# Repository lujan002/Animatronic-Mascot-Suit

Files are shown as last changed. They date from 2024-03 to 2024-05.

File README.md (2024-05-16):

# Junior-Jay Animatronic Mascot 

Watch overview video [here](https://youtu.be/p1z4z74mzpA)

The scope of this project was to develop a wearable, Disney-style, animatronic suit with actuated facial features for the University of Kansas's flagship line of "Jayhawk" mascots. The project was sponsored by the Mechanical Engineering Department at the University of Kansas, with the primary client being the University of Kansas head mascot coach. The initiative aimed to revolutionize the university's mascot program by incorporating advanced, expressive features into a new mascot called "Junior Jay". The primary requirements outlined by the client included the ability for the mascots to display a wide range of dynamic, real-time facial expressions, like those seen in professionally animated characters. 

<p align="center">
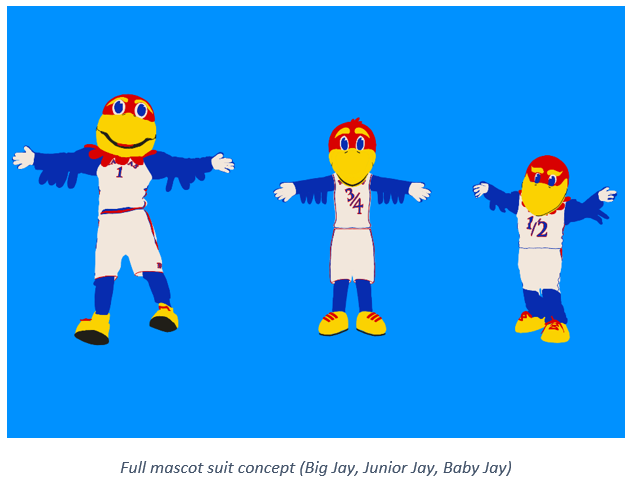
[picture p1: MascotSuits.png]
MascotSuits
  
</p>

Designing an entirely new mascot head from the ground up was not feasible for the financial and time contraints of this project, so the University of Kansas athletics department graciously donated a retired "Baby Jay" mascot head for the team to retrofit into a proof-of-concept prototype for Junior Jay. Without their support, this project would not be possible. 

This project provided a great mix of mechanical, electrical, and software engineering challanges. The engineering objectives were to modify this retired mascot head with seamless control of the mouth, eyebrow, and eyelid actuation mechanisms using custom facial expression detection & control software, while maintaining durability, comfort, and ease of use. The project started in Aug. 2023 with initial drafts of mechanical models, code, and electrical schematics, then concluded in late Apr. 2024 with a functional protoype that met the majority of our project objectives. Below will be an outline of the final state of these three systems. 

<p align="center">
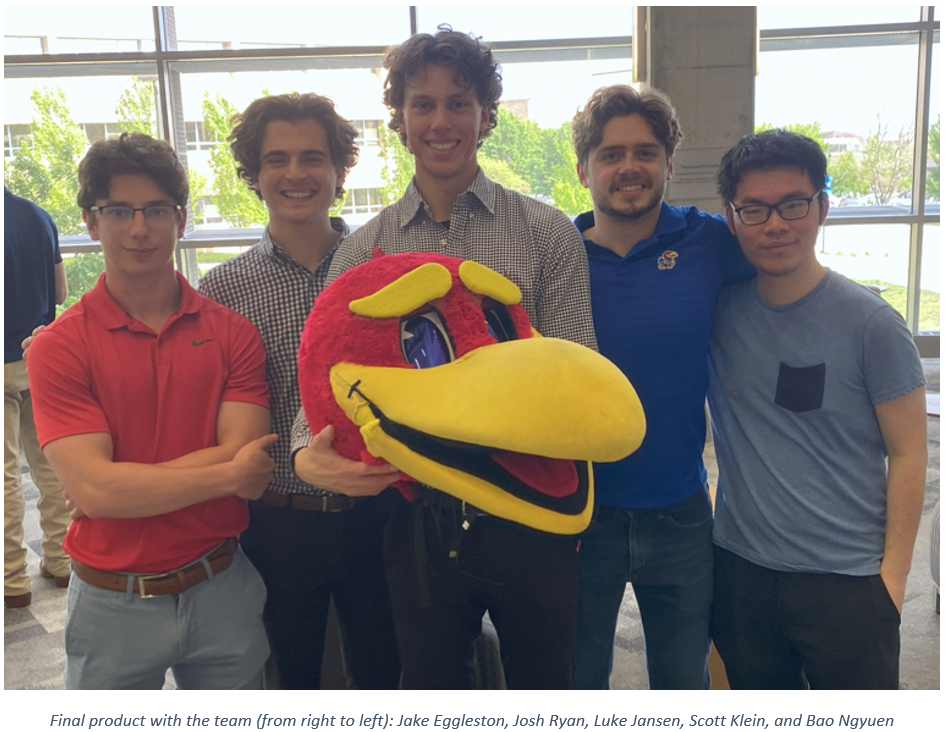
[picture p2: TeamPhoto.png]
TeamPhoto
  
</p>

## Mechanism Sub-Systems
### Beak  

Goal: Open/close beak to simulate smile, shock.

The beak assembly consisted of a lightweight aluminum frame inserted into the original, detached foam beak to provide rigidity and a means for the servo motors to drive the beak. We selected servos rated for 45 kg·cm of torque, suitable for the high-torque demands of our application. This choice was driven by the requirement to counter the beak weight of 0.7 kg (6.87 N), with center of gravity centered 230 mm away (1.58 Nm Torque). After installation, the foam beak was re-stitched to the rest of the head for aesthetic purposes. A primary focus was on ensuring robustness and minimizing weight, and the final frame design shown below was no more than 0.4 kg. 

<p align="center">
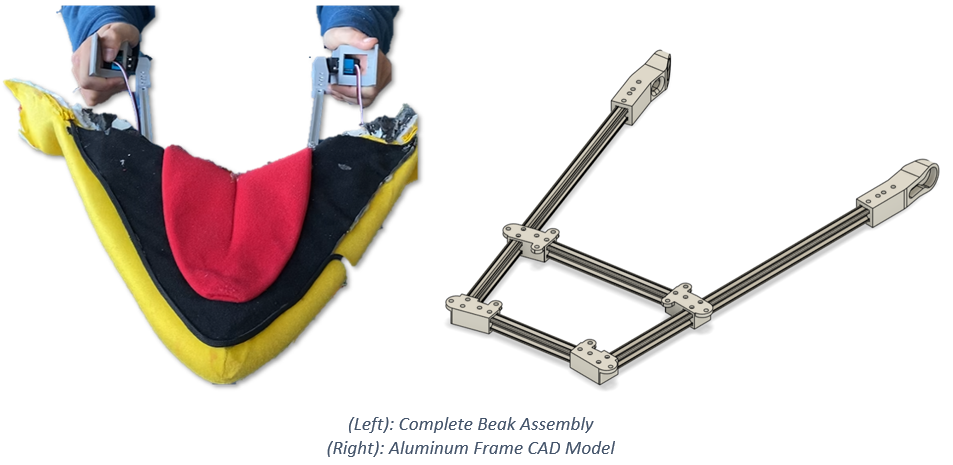
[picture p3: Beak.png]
Beak
  
</p>

### Eyebrows  

Goal: Rotate eyebrows to display nuanced emotions. 

To enable the mascot to express nuanced emotions, precise control over the eyebrows was essential. The final design acheived this by incorporating each eyebrow as one of the links in a three-bar linkage driven by two servos. This gave each eyebrow two ways to pivot, and thus 2 DOF. Each servo connects to one of the other two links, one which keeps its pivot at a fixed distance, and one wich has a slider cutout that allowed for its pivot to translate back and forth. The result is that the eyebrow can raise and lower itself without changing the angle it is oriented at (thus height and angle can be controlled separetely). Given the aesthetic design constraints, the eyebrow actuation mechanisms were concealed inside the head and behind the eyebrow. This in turn necessitated custom-printed shaft extentions so the servo shafts could reach through small holes in the forehead to connect to the links on the outside of the head. Press-fit threaded inserts and a star pattern connection on the shafts ensured the arms did not slip.

<p align="center">
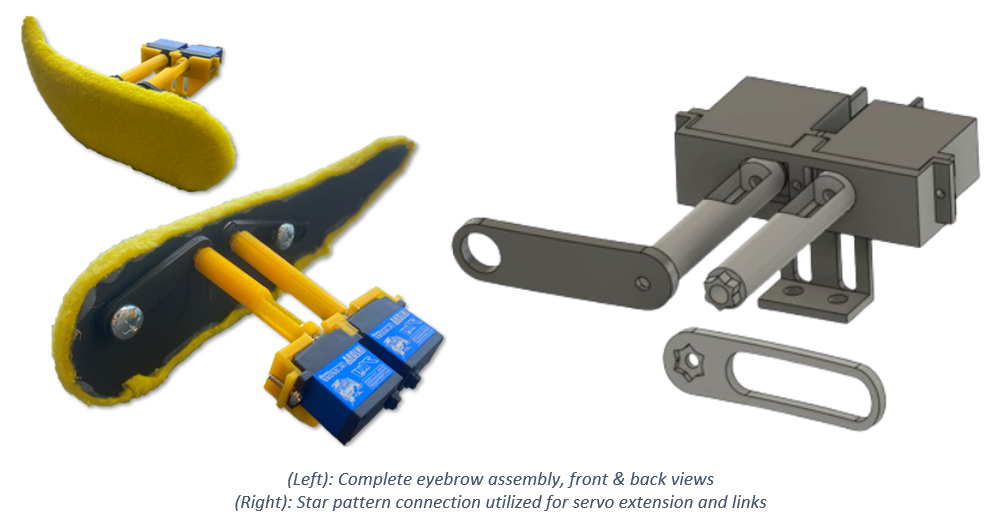
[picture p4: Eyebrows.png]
Eyebrows
  
</p>

### Eyelids  

Goal: Open/close eyelids to simulate blinking.

To enable the animatronics' eyelid functionality, the eyes of the original mascot head had to be removed and offset a small distance to give space for the eyelid fabric to operate. The opportunity to fully rework the eye design was taken. This process involved vacuum forming a PETG plastic sheet over a 3D printed buck, which was then painted with a one-way reflective mirror coating. This new eye was mounted to a frame, along with, conveniently, all the eyelid actuation mechanicms and even the eyebrow servos. This allowed for easy removal of the whole assembly when maintentnce was required. The frame was designed to support the eyebrow mechanics while providing enough space for the eyelid material to spool without increasing in diameter. For eyelid actuation, a compact timing belt system was chosen instead of gears or chains due to its reliability and quiet operation (similar to those used in 3D printers). The eyelid fabric was stiched directly to the belt. 

Initially, a DC motor was considered for this system, but its torque, size, and control limitations led to the selection of a continuous servo motor, which offers sufficient torque and simpler control. To compensate for the servo's slower speed, a gear system was incorporated to increase the speed of the eyelid movement while maintaining the necessary torque for smooth operation. Unlike a normal servo, the continuous servo has no positional feedback. To work around this, two limit switches were added to shut off the motors when tripped. A small object stiched to the belt would trip one switch when the eye was fully open, and the other when fully closed, thus shutting off the motors. 

To better understand how this system works, please watch the docummentation video linked earlier. 

<p align="center">
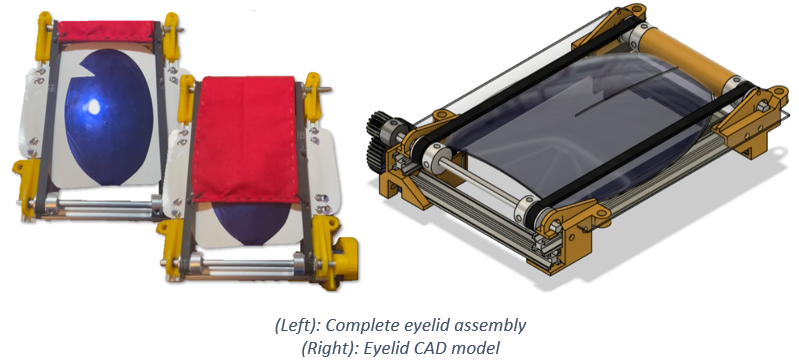
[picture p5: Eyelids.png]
Eyelids
  
</p>

## Expression Detection & Control Software 

Arguably the part of this project with the most innovative potential, and deviation from traditional animatronic models, is the integration of facial detection technology to control the mechanical systems described above. The software algorithm is actually a single “master” python script (master_script.py) running on the Raspberry Pi, which 
handles everything from the capturing of video frames, detection of faces, prediction of a facial expression, and sending of signal to the motors to adjust servo angles to mimic the detected expression.

Early in the development process, it was decided that due to computational limitations of the Raspberry Pi and to avoid jittery mechanical movements, the software would predict discrete emotions and control the motors in set configurations. The emotions to be predicted were "neutral", "angry", "happy", "surprised", and "sad". Separetely, the mouth and eyes would be predicted as "open" or "closed". This approach was chosen over a design that would mimic every nuanced movement of the wearer, prioritizing smooth and stable operation of the mascot.

<p align="center">
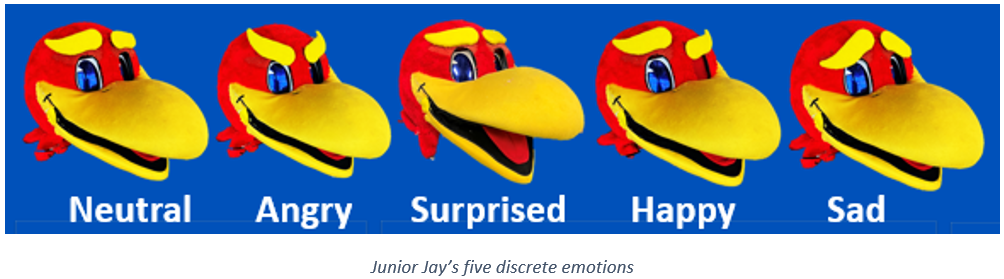
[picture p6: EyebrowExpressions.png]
EyebrowExpressions
  
</p>

The facial detection was naturally split up into different sections based on the mechanical sub-system that it would control. For control of the eyes and mouth, first open-source computer vision libraries were used to extract the coordinates of the facial landmarks (eyes and mouth in this case). Expressions were then classified by measuring the distance between a select few coordinates, such as the outer-most and upper/lower-most mouth edges, and calculating an aspect ratio (mouth height/mouth width). Naturally, when the eyes or mouth are closed, this aspect ratio decreases. Thus, a certain empirically determined ratio was selected and compared with each incoming frames to label the mouth/eyes as "closed" if below the threshold, and "open" if above the threshold. The method implemented in the final master script uses the dlib facial landmark model, although Google's MediaPipe model was also considered.

<!-- Insert EAR,MAR picture here  -->

The movement of the eyebrows, arguably the most important mechanical sub-system in dynamic emotion display, was more intricate. Two approaches were tested for detecting the wearer's emotion out of the five discrete emotions. The first approach used a similar approach to the mouth and eye detection, this time using the eyebrow facial landmark coordinates to come up with some ratio. This posed a more tricky problem that with the eyes and mouth however, as it was quickly realised that predicting emotions based on the eyebrows alone for emotions like sad, happy, and neutral were quite subtle. It would have been possible to combine the eyebrow ratio with a ratio for other landmarks on the face, but ultimately it was decided that a more effective approach would be to use an image classification model to predict discrete emotions. 

A convolutional neural network (CNN) was trained on the [FER-2013 dataset](https://www.kaggle.com/datasets/msambare/fer2013) (Facial Emotion Recognition) to classify facial expressions. The training process is documented in train-emotion-detection.py. The original pre-trained model is attached directly as model_optimal2.h5. This model was converted to a tensorflow.lite model (saved as model.tflite in convert_to_tflite.py), which is directly used in master_script.py. Readers interested in the implementation of this model, its archeture, or the training process are encouraged to reveiw these scripts. The model achieves over 75% accuracy on the validation dataset, with even better performance observed in practical use (potentially a result of the FER-2013 dataset's well-known problem with inconsistent labeling). 

<p align="center">
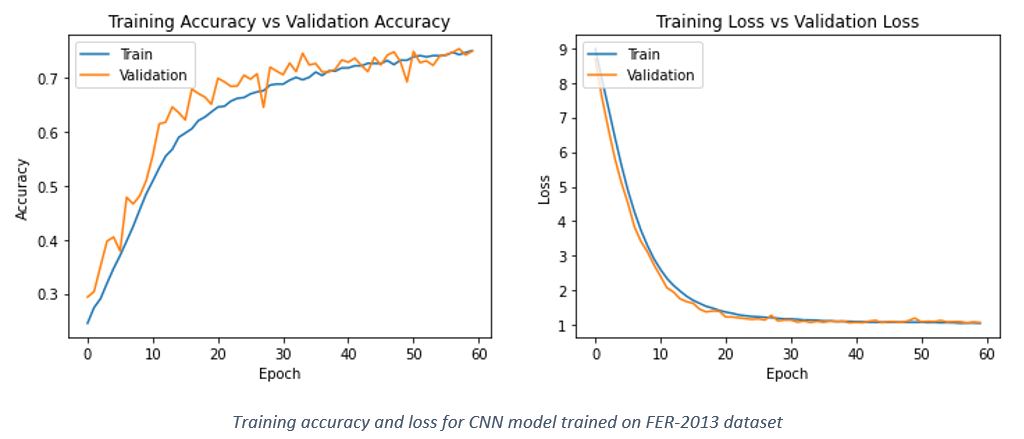
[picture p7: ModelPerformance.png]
ModelPerformance
  
</p>

In order to ensure the program could run as close to real-time as possible, steps were taken to reduce the computational load. One simple approach used was to limit the number of frames processed. Several different frame rates were tested, and ultimately 5 fps was chosen as a nice balance between computational low cost and quick enough updates. The images were also converted to greyscale before processing, which is what the model was trained on and also happens to be more computationally efficient. The model was run using Google’s TensorFlow.Lite library, which is purpose built for running models on lighter hardware. Challenges in detecting faces within the dark, close-up environment inside the mascot's head, even with the use of a low-light, wide-angle camera, hindered the successful demonstration of the internal camera functionality. Efforts to improve face detection under these conditions included enhancing illumination and artificially padding the frame borders to create the illusion of a more distant face. For our demonstration purposes, the camera was positioned outside the head. Future work is required to fully achieve the project's initial objectives under these specific conditions. 

<p align="center">
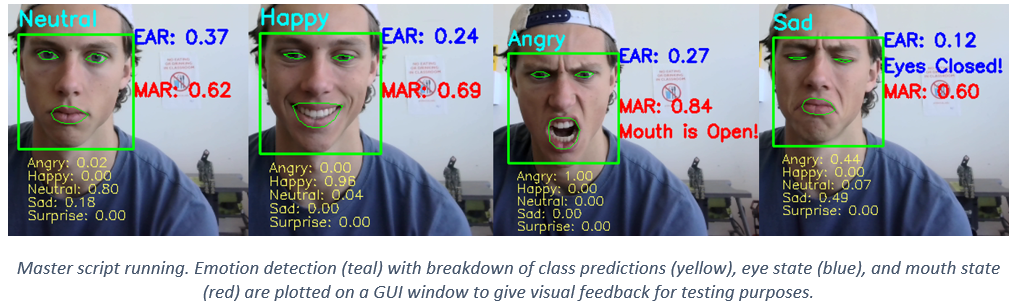
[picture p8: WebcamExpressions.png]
WebcamExpressions
  
</p>

Whatever the approach, signals to the servos were sent from the designated GPIO pins using the pigpio library. 
<!-- Readers can test the standalone software functionality by installing the packages in requirements.txt and runnign software_demo.py -->

## Electrical System

The electrical system composed of 50,000 mAh battery pack specifically chosen for a 2hr. lifetime (or that of a typical basketball game), its three USB type A and C ports, and its 5-20V capacity. This battery choice was driven by the aforementioned 45 kg·cm servos we selected required 9V power to achieve our torque target. Two HUSB238 power delivery breakouts configured to draw 5V and 9V respectively were connected the USB ports on the battery. The Raspberry Pi was directly connected to the third port. In this configuration, all the servos requiring 5V (eyelid and eyebrow servos) were powered separately from the 9V servos (beak servos). Miscellaneous components such as the eyelid limit switches, fans, camera, and LED indicator panel were to be powered by the Raspberry Pi.  

There were two key considerations when designing this system. This system contains approximately fifty loose wires, and it quickly became apparent that wire management was crucial for easy maintenance, visibility inside the head, and ensuring the integrity of the sensitive wiring. All wires were strategically routed around the internal structure of the head. Wires were systematically braided and grouped by sub-system, labeled, and secured to prevent obstruction of vision, reduce tangling risks, and simplify maintenance procedures. A Raspberry Pi GPIO pin extension board with screw clamps was used and gave much needed easy accessibility when pulling and plugging wires. A power bus was designed and implemented that handled the distribution of power to all motors in a convenient location. Since these electrical components would be operating very close to a human’s face, safety was also a top priority. Initial testing done on the 9V beak servos under high load produced worrying results on the multimeter. In some cases, the current draw of an individual servo could spike to well over 1A. To prepare for dangerous current spikes like this, two 1Ω power resistors in series were added to the 9V rail on the power bus to dissipate any excess current as heat. An emergency safety switch was also added to shut the 9V motors off.  

<p align="center">
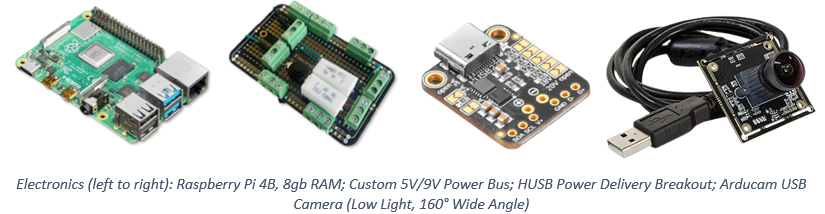
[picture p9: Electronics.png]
Electronics
  
</p>
<p align="center">
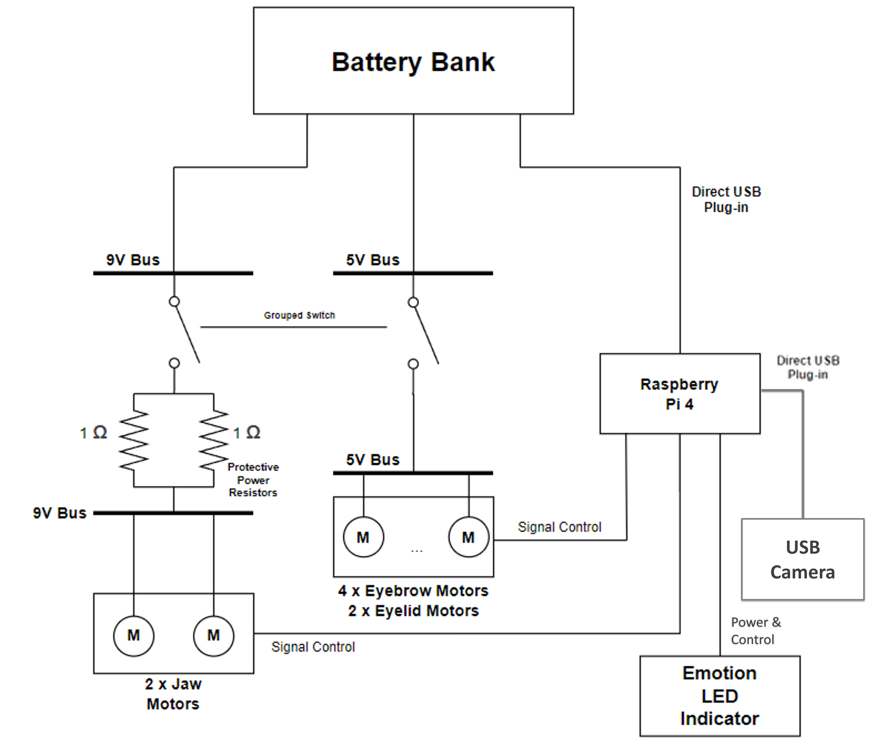
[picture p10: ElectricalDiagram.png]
ElectricalDiagram
  
</p>

### Voltage Converter PCB
The servos that move the lower beak were chosen for their high torque at operating volages above 5V. The servos used were actually rated for 5V - 8.4V, so initially a voltage converter circuit was designed to step down the input voltage to 8V. Later it was realized that the servos could run on 9V directly from the power bank, making this voltage converter irrelevant. Regardless, an short summary of the work done on it will be listed. A [dummy breakout](https://www.adafruit.com/product/5807) was used to draw 12V from the [power bank](https://www.amazon.com/Charging-50000mAh-Portable-Compatible-External/dp/B0C5D1JR2K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), which was further stepped down to 8V by this circuit. 

The schemetic shown below incorporates an [LM317 Voltage Regulator](https://www.ti.com/product/LM317-N/part-details/LM317T/NOPB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) ([footprint](https://www.snapeda.com/parts/LM317T/NOPB/Texas%20Instruments/view-part/)) and a series of commonly available resistors.

The board was designed in KiCAD and printed at the school shop.

<p align="center">
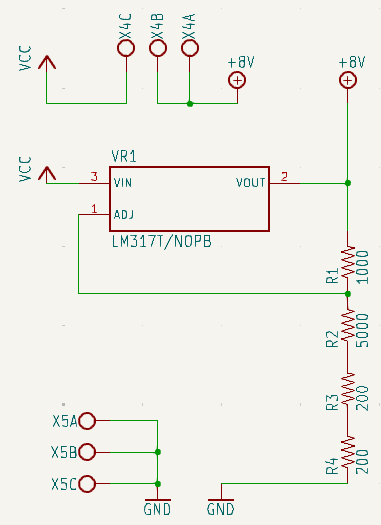
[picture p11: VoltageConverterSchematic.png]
VoltageConverterSchematic
  
</p>
<p align="center">
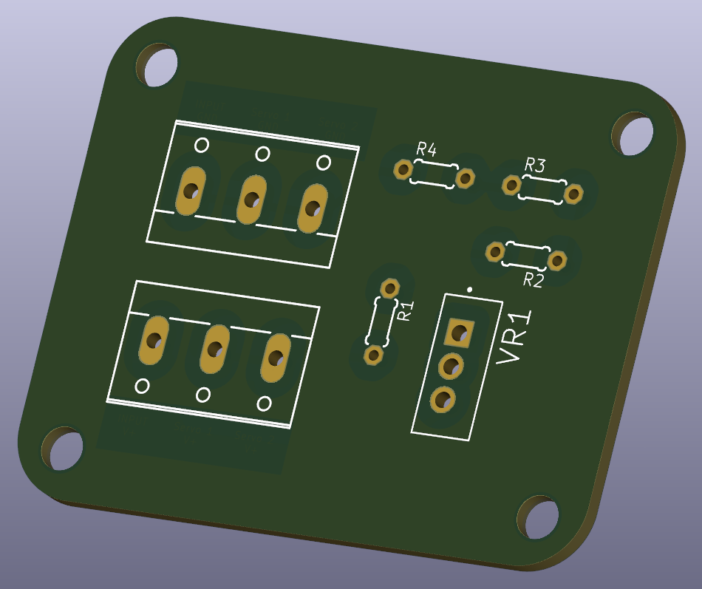
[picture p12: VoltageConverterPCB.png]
VoltageConverterBoard
  
</p>

### Emotion LED Indicator Panel
One concern during operation of the animatronic was that the wearer would have no idea what expression was currently being used. The beak and eyelids would be obvious enough to the wearer if they were open or closed, but there would be no way of knowing the current state of the eyebrows. An LED panel indicator panel was designed as a solution to this. The panel was planned to be mounted inside the head and include seven LEDs, five for each of the discrete emotions, one LED for the mouth state, and one for the eye state. This would tell the wearer inside if the expression detection program is working as intended. Ultimately time constraints prevented the implementation of this optional feature, but the concept was proven to work. 

The board was designed in KiCAD and printed at the school shop.

<p align="center">
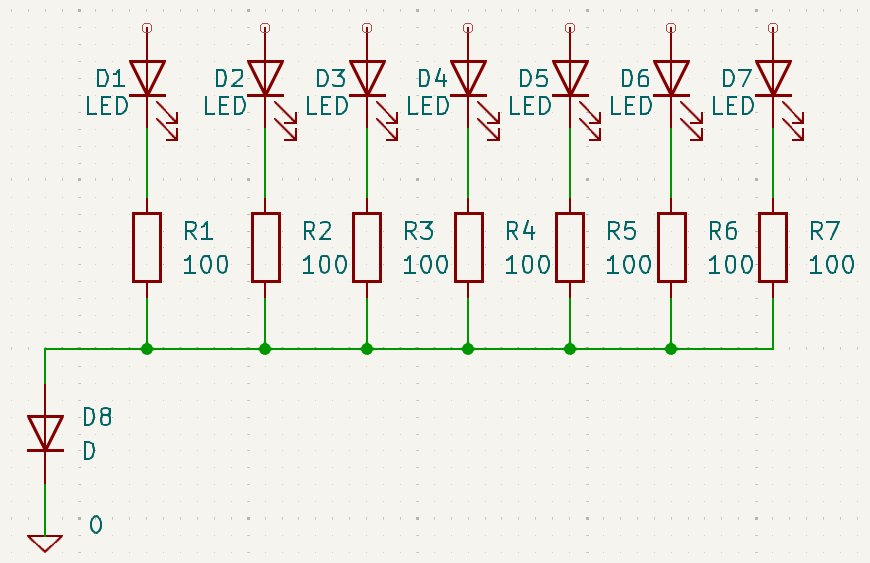
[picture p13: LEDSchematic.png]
LEDSchematic
  
</p>
<p align="center">
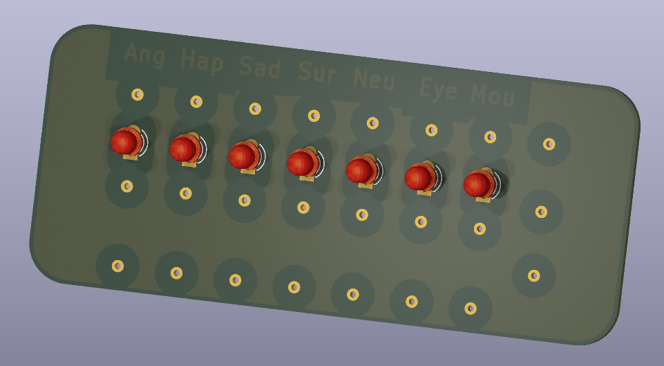
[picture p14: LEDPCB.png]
LEDPCB
  
</p>

### Future Work

While the project has made significant strides in demonstrating that the functionality and appeal of university mascots can be dramatically improved, there remains scope for further development to fully realize the envisioned goals. Future work could focus on several areas to refine and expand the project's achievements: 

1.  Refinement of Mechanical Systems: Further refinement of the mechanical systems controlling facial expressions is essential. Continuous testing and iteration could lead to more fluid and natural movements, reducing any mechanical lag or stiffness currently present. 
2.  Advanced AI and Machine Learning: Implementing more sophisticated AI algorithms and machine learning techniques, such as training on a larger dataset or a custom dataset built to our specific needs, could enhance the accuracy and responsiveness of the facial recognition system. Also, work can be done to give more nuanced expressions prediction rather than the simpler discrete expression approach used. This would ensure a more precise and seamless translation of the performer’s expressions to the mascot. 
3.  Enhanced Cooling Technologies: Although the current cooling system provides basic relief, exploring advanced technologies like phase change materials or more efficient heat exchange mechanisms could offer better temperature regulation, increasing comfort during longer performances or in more extreme weather. 
4.  Integration of Interactive Technologies: Adding interactive technologies such as voice modulation and responsive sound systems could make the mascots even more engaging. For instance, allowing the mascots to respond vocally to crowd interactions or integrate sound effects linked to their movements could greatly enhance audience interaction. 
5.  Sustainability and Materials Science: Investigating more sustainable materials and construction techniques that maintain durability while reducing weight could improve the ergonomics and environmental impact of the mascot costumes. 
6.  Extended Wearability Studies: Conducting extended wearability studies to gather data on the performer's comfort and suit ergonomics over longer periods can provide insights into necessary adjustments and improvements. 
7.  Scalability and Transferability: Finally, considering how these enhancements can be standardized and transferred to other mascot programs could broaden the impact of the project. Developing a modular system that can be customized and adapted to different mascots could make these advancements more accessible to other institutions. 
8.  Foolproof electrical safety measures: A mechanical cover should be added to cover the power bus to protect against accidental contact and reduce the risk of short circuits. Additionally, wiring may be optimally routed inside the head wall to minimize exposure and vulnerability. Safety devices such as fuses, and micro-circuit breakers will be incorporated to prevent electrical overloads and potential hazards.  

These areas of future work would not only address the remaining challenges, but also push the boundaries of what is possible in mascot design and performance - potentially setting new industry standards. 

For a full detail of the technical work involved in the project, please refer to the "Junior Jay Final Poster" and "Junior Jay Final Report" documents.

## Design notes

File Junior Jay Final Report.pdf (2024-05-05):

Title: Junior Jay Capstone Project Sponsor: The University of Kansas School of Engineering Mechanical Engineering Members: Scott Klein, Luke Jansen, Josh Ryan, Jake Eggleston Electrical Engineering Members: Caleb Meyer, Bao Nguyen, Josie Harding

1

## Table of Contents

Figure 1. Use This Format to Label All Figures!! | Error! Bookmark not defined.

Electrical Engineering Members: Caleb Meyer, Bao Nguyen, Josie Harding

2

## Executive Summary

### Motivation

After observing the KU mascots in action, two members of our project sent a proposal to the University of Kansas on June 23, 2023, seeking to enhance the Big Jay and Baby Jay mascots by adding Disney-like animated features and a liquid cooling garment for performer comfort. This initiative aimed to boost the mascots' appeal during key events like March Madness. However, the head mascot coach suggested creating a new mascot, Junior Jay, for the kids club of Kansas Athletics, to preserve the originality of Big and Baby Jay.

### Engineering Objectives

In response to the head mascot coach's suggestion, our team planned to integrate AI-driven facial recognition technology with mechanical systems for the Junior Jay mascot. This setup would detect and mimic the facial expressions of the person inside the mascot head in real time, translating them into movements of features like eyebrows, eyelids, and mouth via actuators and linkages. This combination of AI and mechanical engineering aims to enhance the mascot's expressiveness and ensure performer comfort during events.

### Technical Approach

To achieve our project goals, our group met weekly throughout the spring semester to develop and refine the designs for the mechanical movements needed to animate the mascot's facial features. We took a prototype and testing approach to develop Junior Jay for this project. To do so, servo motors and 3D-printed linkages were utilized and optimized for seamless integration and effective operation. During the installation phase, we performed additional redesigns to ensure the components fit well within the mascot head while maintaining comfort and wearability for the performer. This iterative design and testing process was vital for balancing functionality and user comfort.

### Results

We successfully met most of our objectives for enhancing the mascot's features, although we encountered challenges with achieving full functionality of the eyelids due to software bugs and mechanical unreliability. In the last few weeks of the project, our team intensified our efforts, focusing closely on collaboration and problem-solving to finalize the enhancements. Our result was a functioning animatronic Junior Jay with facial recognition capabilities. Despite the issues with the eyelids, our commitment in the final stages ensured that the rest of the features, including the expressive eyes and integrated cooling system, were implemented effectively. This teamwork and determination were crucial in bringing our innovative mascot enhancements to near completion, significantly elevating the mascot's functionality and appeal.

### Summary

Our project achieved substantial progress in enhancing the mascot's animated features, though some challenges, like the full functionality of the eyelids, remain. Recognizing the potential to fully realize our vision, we submitted a proposal to continue our work, aiming to deliver a completely functional mascot head. This ongoing effort will focus on resolving existing issues and refining the design to ensure it is event ready. We recommend future teams prioritize software optimization and consider further

Electrical Engineering Members: Caleb Meyer, Bao Nguyen, Josie Harding

3

ergonomic adjustments to improve performer comfort. These steps will help in achieving a pioneering mascot presence at university events, greatly enhancing both performance and spectator experience.

Electrical Engineering Members: Caleb Meyer, Bao Nguyen, Josie Harding

4

## Introduction

### General

This project was sponsored by the Mechanical Engineering Department at the University of Kansas, with the primary client being the KU mascot coach. The initiative aimed to revolutionize the university's mascot program by incorporating advanced, expressive features into the Big Jay and Baby Jay mascots. Inspired by the intricate articulation of iconic characters such as Disney's Mickey and Minnie Mouse, the enhancements were intended to include a range of animated facial expressions and integrated cooling systems to ensure performer comfort during performances, especially in warm conditions. This effort aligns with the university's broader goals of enhancing school spirit and audience engagement during athletic events and other university functions. The project's strategic objective was to significantly elevate the visibility and interactive capability of the mascots, thereby enriching the fan experience and potentially increasing student and community involvement with Kansas Athletics.

### Motivation

The motivation for this project stemmed from a desire to enhance the interactive capabilities and overall appeal of the University of Kansas mascots, Big Jay and Baby Jay, as expressed by the client, the KU mascot coach. The primary requirements outlined by the client included the ability for the mascots to display a wide range of dynamic, real-time facial expressions, like those seen in professionally animated characters. This enhancement was aimed at fostering a more lively and engaging presence at university events, thereby deepening the emotional connection between the mascots and the audience. Additionally, the client emphasized the need for improved comfort for the mascot performers, particularly during the intense heat often experienced during early season football games and other outdoor activities. This led to the requirement for integrating advanced cooling technologies within the mascot suits, specifically through the development of a Liquid Cooling Garment system that could maintain a comfortable temperature for the performers over extended periods.
These enhancements were expected to boost the morale and performance of the mascot team and to serve as a pioneering model for other universities looking to upgrade their mascot programs. The overarching goal was to create mascots that are not only emblematic of KU spirit but also stand out on a national level during high-visibility events such as March Madness, thereby attracting more attention and potentially increasing enrollment and fan support. This project was also seen as a strategic move to innovate within the realm of collegiate mascots, pushing the boundaries of mascot interaction and performance.

Electrical Engineering Members: Caleb Meyer, Bao Nguyen, Josie Harding

5

### Engineering Objectives (or Project Design Requirements)

The engineering objectives for this project were defined to directly address the customer requirements and ensure a high level of performance and innovation in the mascot enhancements. The primary design requirements included:

1. Facial Expression Animation: The mascots needed to be capable of displaying a variety of facial expressions that mimic human emotions. This required the development of a sophisticated mechanical system within the mascot heads, utilizing servo motors, sensors, and 3D-printed components to animate features like the eyebrows, eyelids, and mouth in real-time.
2. Facial Recognition Integration: To achieve real-time mimicry of the performer’s expressions, an AI-driven facial recognition system was required. This system would interpret the performer's facial expressions captured via an internal camera and translate them into mechanical movements, ensuring that the mascot's external expressions reflect those of the performer inside.

### 3. Cooling System Implementation: Given the physical exertion and heat exposure during

performances, integrating a Liquid Cooling Garment (LCG) was essential. This system needed to be seamlessly incorporated into the mascot suit, providing efficient heat exchange without adding significant weight or restricting the performer's movements.
4. Durability and Comfort: All enhancements had to be designed with durability and comfort in mind. The mechanical components and cooling systems needed to withstand the rigors of performances and be easy to maintain. Moreover, the overall design had to ensure that the weight distribution and ergonomics of the mascot suit did not compromise the performer’s comfort or mobility.

### 5. Ease of Use and Maintenance: The systems developed for the mascots needed to be user-

friendly, allowing quick adjustments and repairs if necessary. This was crucial for ensuring that mascot handlers could manage the technology effectively during events without requiring specialized knowledge.

These engineering objectives were crafted to create a mascot experience that was not only more engaging and enjoyable for audiences but also more manageable and comfortable for performers, setting a new standard for mascot design in collegiate sports.

Electrical Engineering Members: Caleb Meyer, Bao Nguyen, Josie Harding

6

## Technical Work

### Technical Approach

Our team took a general engineering design approach with this project. Throughout the project, our team met in weekly meetings to discuss and design Junior Jay. Phase 1 included concept design where our team defined the problem statement, product design specification, engineering objectives, and concepts to satisfy those engineering objectives. Phase 2 involved embodiment design where Junior Jay was broken down into three sections: mechanical, electrical, and software. Mechanical systems included design of the beak, eyebrows, and eyelids. Electrical systems included development of the main CPU being the Raspberry Pi, power, power block, and camera. Software included facial recognition to input facial expression signals and output a signal to the mechanical system. With these three sections, modeling, sizing of parts, prototyping, and testing occurred. Our team designed, iterated, and tested Junior Jay was fully functioning. Lastly, phase 3 included detail design where all the sections of Junior Jay were finalized installed into the head as a final product.

### Experimental Setup / Numerical Setup / Designs

Beak
In the design of the mechanical mechanisms for our animatronic Jayhawk head, a primary focus was on ensuring robustness and minimizing weight. One critical component was the beak actuation mechanism, which required careful consideration due to the forces involved, particularly gravity. The beak assembly (figure 1) consisted of an aluminum frame inserted into it to provide rigidity and a point for the servo motors to drive the beak. To achieve reliable operation, we selected servo motors capable of delivering high torque. Specifically, we used servos rated for 45 kg·cm of torque, suitable for the demands of our application.
The beak itself has a mass of 0.36 kg (Figure 3), and the aluminum frame increased the mass to 0.7kg. Through a simple finger-balance test, we determined its center of gravity to be approximately 230 mm (9 inches) from the motor's pivot point. Given this configuration, the required torque to move the beak was calculated as follows:
Torque τ is given by τ = r · F, where r is the radius (distance from pivot), and F is the force due to gravity acting on the mass.

Converting the mass of the beak into weight using the acceleration due to gravity (g=9.81 m/s^2):

F = m · g = 0.7 kg · 9.81

m
s

= 6.87 N

The lever arm r is 0.230 m (230 mm). Thus, the required torque is:

τ = 0.230 m · 6.87 N = 1.58 N · m

Electrical Engineering Members: Caleb Meyer, Bao Nguyen, Josie Harding

7

Each servo, providing 4.41 Nm (45 kg·cm), and with two servos employed, yielded a total available torque of 8.82 Nm (90 kg·cm). This is significantly more than the required 1.58 N·m, ensuring that the servos can operate the beak with high reliability and responsiveness, even under additional load, external forces, or in the event one motor fails.

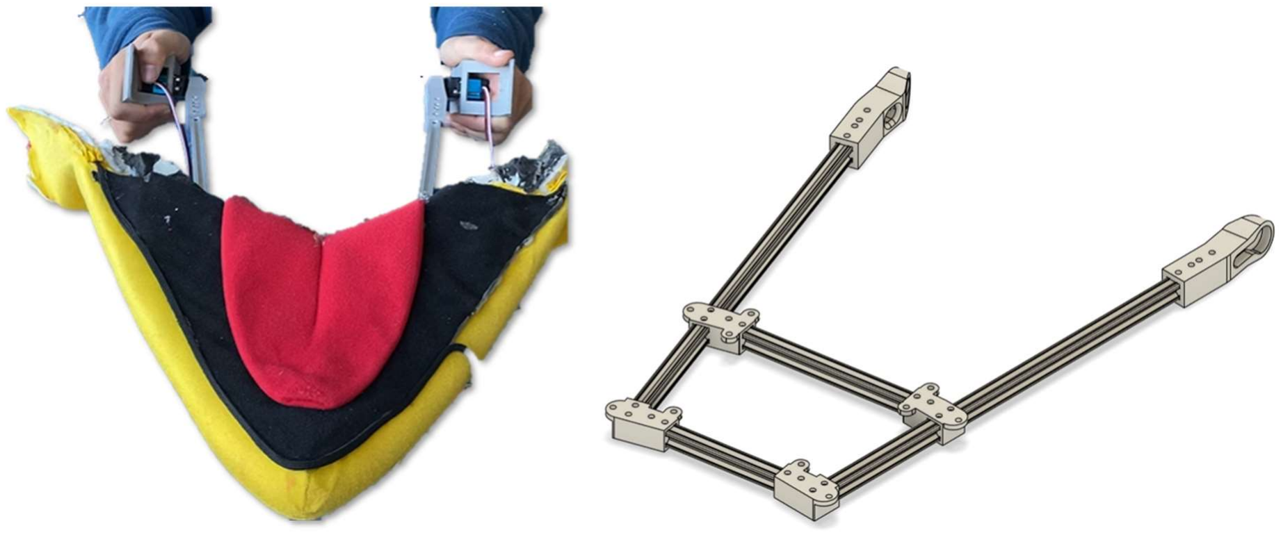
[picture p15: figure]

Figure 1 (Left): Complete Beak Assembly Figure 2 (Right): Aluminum Frame CAD Model

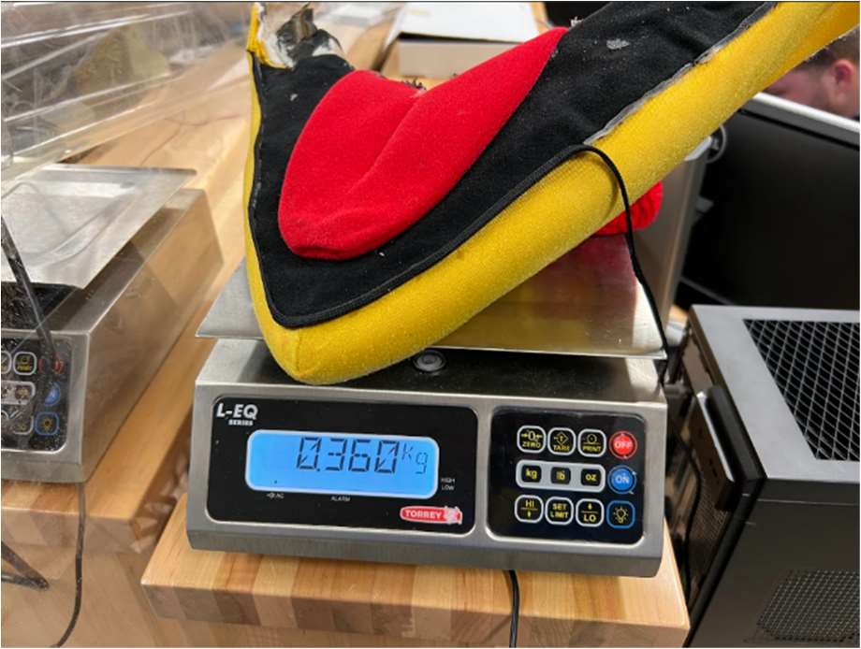
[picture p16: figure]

Figure 3: Jaw mass (without Al Frame)

Eyebrows
To enable the mascot to dynamically express emotions, precise control over the eyebrows was essential. Given the design constraints that the eyebrow actuation mechanisms must remain concealed, the servos were hidden inside the head. Initially, a simpler design featuring a single rotation point at the center of each eyebrow was considered. This would have only required one servo motor for each eyebrow, but ultimately, we settled on a slightly more complicated design that used two servos and incorporated the eyebrow as a three-bar linkage (figure 4). The benefit to this design was that there

Electrical Engineering Members: Caleb Meyer, Bao Nguyen, Josie Harding

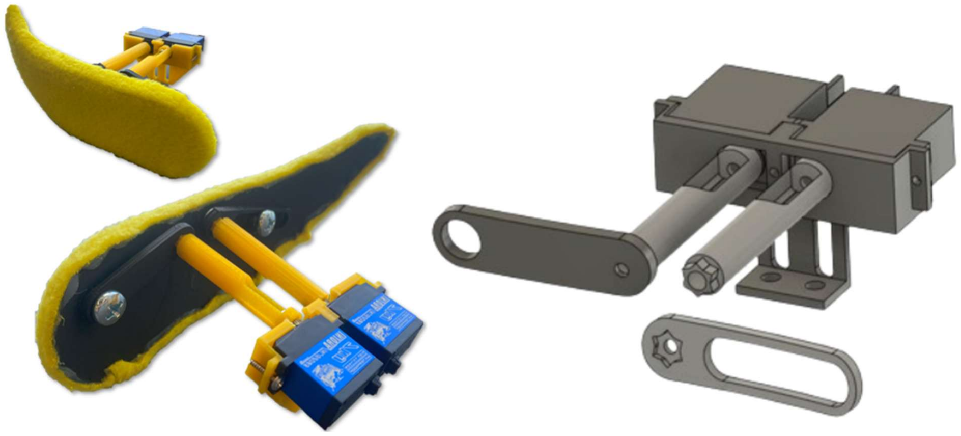
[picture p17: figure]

8

were now two pivot locations, enabling the eyebrow to raise and lower itself without changing the angle it was oriented at. The servos were conveniently mounted to the eyelid Al frame. These servos had shaft extensions that protruded through the forehead by way of two small holes. The arms were fastened into these extended shafts, which had press-fit threaded inserts and a star pattern connection interface (figure 5) to ensure the arms would not slip. One arm kept its pivot at a fixed distance, while the other had a slider cutout which allowed for its pivot to translate back and forth. This combined setup allowed for free rotation and translation eyebrow. The arms are completely hidden behind the eyebrow and colored the same as the eyebrow for camouflage and redundancy.
The installation and calibration of the eyebrows, essential for achieving precise expression angles, involved attaching the arms at the same angle the servo shaft was set to. To facilitate this process, a Python script was developed which could directly control each eyebrow servo via a simple slider interface through a serial connection with the Raspberry Pi. This allowed for precise adjustment and easy selection of the optimal angles for expressing different emotions. After fine-tuning the servos to the desired positions for each emotion using a practical approach, the angles were recorded and integrated into the master script for consistent application.

Figure 4 (Left): Complete eyebrow assembly, (top: front view, bottom: back view) Figure 5 (Right): Star pattern connection utilized for servo extension and links

Eyelids
To improve the animatronics' eyelid functionality, a new eye design was developed using SLA 3D printing, creating a smooth surface that allows for uninterrupted eyelid movement (figure 6). This process involved vacuum forming a PETG plastic sheet over the 3D printed model to ensure minimal material friction and enhance performance. For precise eyelid motion, a compact timing belt system was chosen instead of gears or chains due to its reliability and quiet operation, similar to those used in 3D printers. The frame was designed to support the eyebrow mechanics while providing enough space for the eyelid material to spool without increasing in diameter. Initially, a DC motor was considered for this system, but its torque, size, and control limitations led to the selection of a continuous servo motor,

Electrical Engineering Members: Caleb Meyer, Bao Nguyen, Josie Harding

9

which offers sufficient torque and simpler control. To compensate for the servo's slower speed, a gear system was incorporated to increase the speed of the eyelid movement while maintaining the necessary torque for smooth operation. Unlike a normal servo, the continuous servo has no positional feedback. To work around this, two limit switches were added so that a the belt system would trip one when the eye was fully open, and the other when fully closed, thus shutting off the motors.

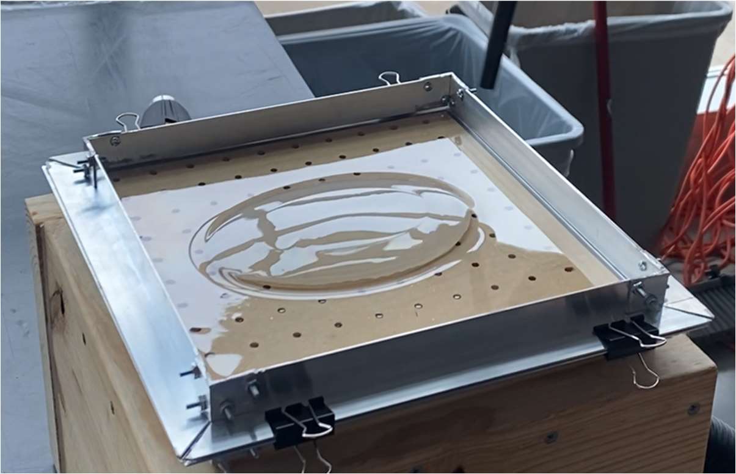
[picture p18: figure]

Figure 6 (Left): Vacuum forming PETG plastic eye

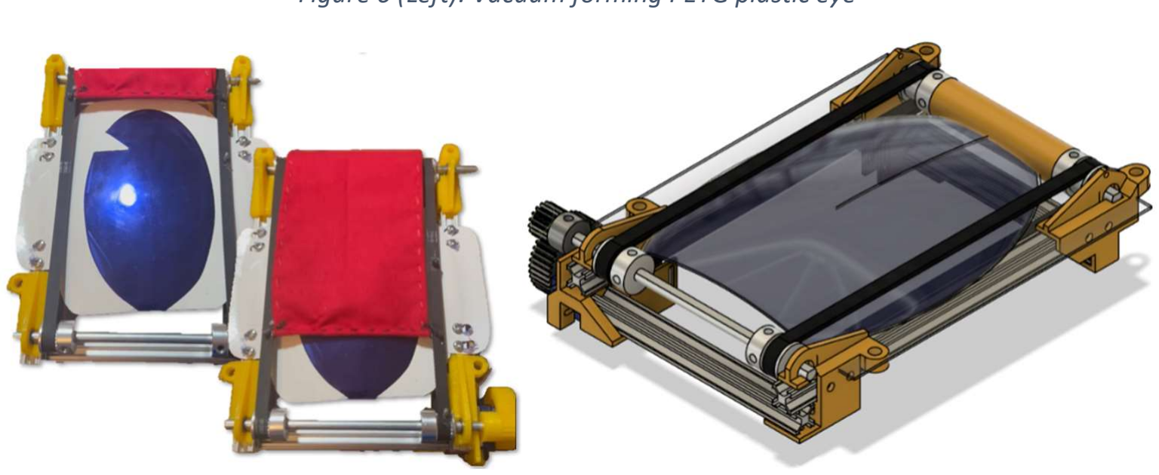
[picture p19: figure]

Figure 7 (Left): Complete eyelid assembly Figure 8 (Right): Eyelid CAD model

Electrical System
The electrical system composed of 50,000 mAh battery pack specifically chosen for a 2hr. lifetime (or that of a typical basketball game), its three USB type A and C ports, and its 5-20V capacity. This battery choice was driven by the aforementioned 45 kg·cm servos we selected required 9V power to achieve our torque target. Two HUSB238 power delivery breakouts configured to draw 5V and 9V respectively were connected the USB ports on the battery. The Raspberry Pi was directly connected to the third port. In this configuration, all the servos requiring 5V (eyelid and eyebrow servos) were powered separately from the 9V servos (beak servos). Miscellaneous components such as the eyelid limit switches, fans, camera, and LED indicator panel were to be powered by the Raspberry Pi.

Electrical Engineering Members: Caleb Meyer, Bao Nguyen, Josie Harding

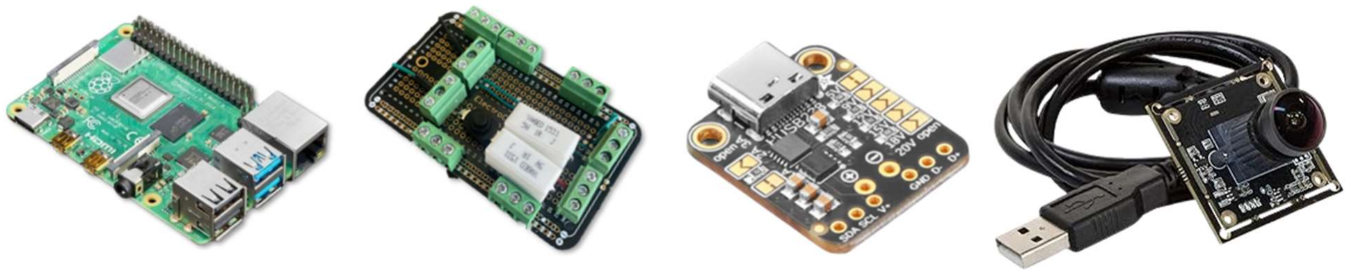
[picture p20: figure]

10

There were two key considerations when designing this system. This system contains approximately fifty loose wires, and it quickly became apparent that wire management was crucial for easy maintenance, visibility inside the head, and ensuring the integrity of the sensitive wiring. All wires were strategically routed around the internal structure of the head (figure 9). Wires were systematically braided and grouped by sub-system, labeled, and secured to prevent obstruction of vision, reduce tangling risks, and simplify maintenance procedures. A Raspberry Pi GPIO pin extension board with screw clamps was used and gave much needed easy accessibility when pulling and plugging wires. A power bus was designed and implemented that handled the distribution of power to all motors in a convenient location. Since these electrical components would be operating very close to a human’s face, safety was also a top priority. Initial testing done on the 9V beak servos under high load produced worrying results on the multimeter. In some cases, the current draw of an individual servo could spike to well over 1A. To prepare for dangerous current spikes like this, two 1Ω power resistors in series were added to the 9V rail on the power bus to dissipate any excess current as heat. An emergency safety switch was also added to shut the 9V motors off.
These efforts not only ensured the operational safety of the animatronic but also enhanced the overall user experience by maintaining clear visibility and ease of use.

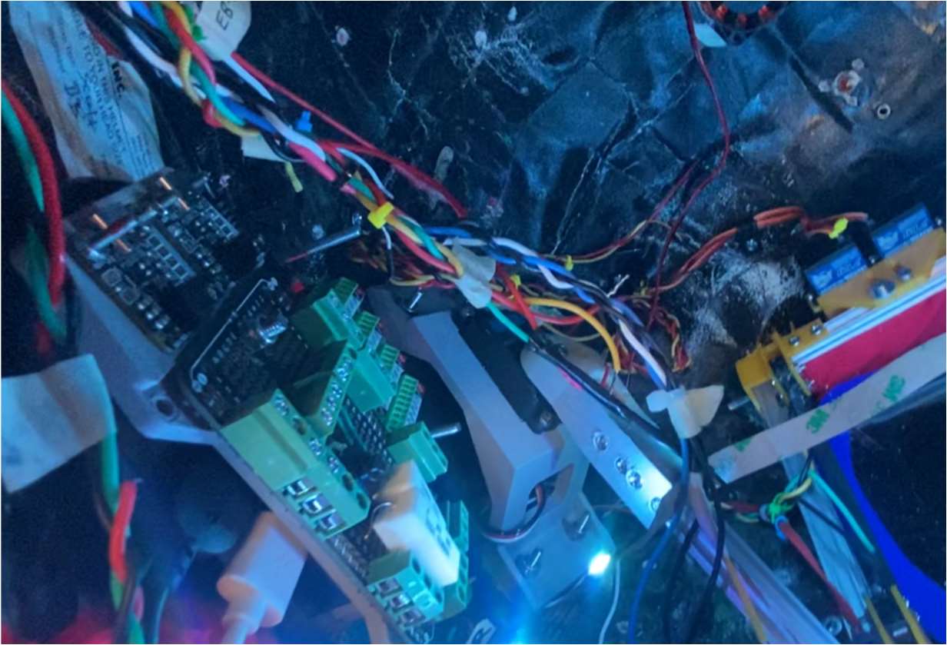
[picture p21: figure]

Figure 9. Wires were braided and routed for easy plug-in

Figure 10. Electronics (left to right): Raspberry Pi 4B, 8gb RAM; Custom 5V/9V Power Bus; HUSB Power Delivery Breakout; Arducam USB Camera (Low Light, 160° Wide Angle)

Electrical Engineering Members: Caleb Meyer, Bao Nguyen, Josie Harding

11

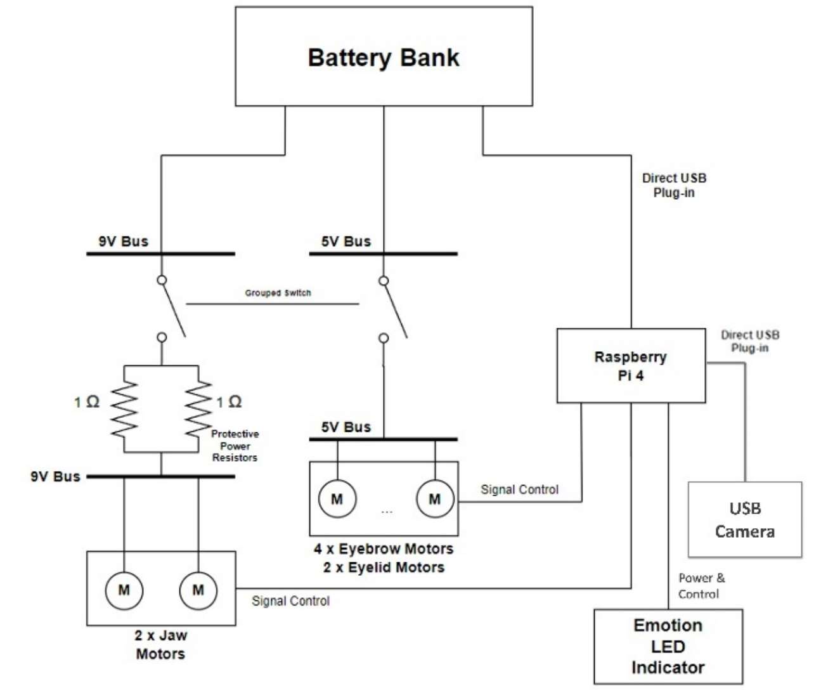
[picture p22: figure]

Figure 11: Electrical System Schematic

Software
A distinctive aspect of this project that underscores its innovative potential, particularly in terms of intellectual property, is the integration of facial detection technology. This software enables the animatronic to interact dynamically with its environment, recognizing and responding to human faces in real-time. This capability not only sets our animatronic apart from traditional models but also opens avenues for patentability due to its unique application in an animatronic context.
The software algorithm is actually a single “master” python script running on the Raspberry Pi, which handles everything from the capturing of video frames, detection of faces, prediction of a facial expression, and sending of signal to the motors to adjust servo angles to mimic the detected expression. Early in the development process, it was decided that due to computational limitations of the Raspberry Pi and to avoid jittery mechanical movements, the software would predict discrete emotions and control

Electrical Engineering Members: Caleb Meyer, Bao Nguyen, Josie Harding

12

the motors in set configurations (figure 12). This approach was chosen over a design that would mimic every nuanced movement of the wearer, prioritizing smooth and stable operation of the mascot. Thus, the facial detection was naturally split up into different sections based on the mechanical sub-system that it would control. For control of the eyes and mouth, first open-source computer vision libraries were used to extract the coordinates of the facial landmarks (eyes, mouth, nose, chin, etc.). Expressions were then classified by measuring the distance between a select few coordinates and comparing them to some empirically determined ratio. This method implemented in the final master script uses the dlib model, although Google's MediaPipe model was also considered.
The movement of the eyebrows, arguably the most important mechanical sub-system in dynamic emotion display, was more intricate. Two approaches were tested for detecting the wearer's expressions as "neutral," "angry," "happy," "surprised," or "sad," based on the distance between the inner brow points. The first approach uses a similar approach to the mouth and eye detection, this time using the MediaPipe or dlib library to extract the eyebrow facial landmark coordinates and calculate certain distances, like the distance between the eyebrows and the aspect ratio.
The second, more effective approach involves an image classification model. A convolutional neural network (CNN), trained on the FER-2013 facial emotion dataset, classifies facial expressions (figure 13). The master script uses this model to predict emotions from the webcam stream. The model achieves over 75% accuracy on the validation dataset (figure 14), with even better performance observed in practical use, potentially a result of the FER-2013 dataset's well-known problem with inconsistent labeling.
Whatever the approach, signals to the motor servos were sent to the designated pins using the pigpio library.
In order to ensure the program could run as close to real-time as possible, steps were taken to reduce the computational load. One simple approach used was to limit the number of frames processed. Several different frame rates were tested, and ultimately 5 fps was chosen as a nice balance between computational low cost and quick enough updates. The images were also converted to greyscale before processing, which is what the model was trained on and also happens to be more computationally efficient. The model was run using Google’s TensorFlow. Lite library, which is purpose built for running models on lighter hardware.
Challenges in detecting faces within the dark, close-up environment inside the mascot's head, even with the use of a low-light, wide-angle camera, hindered the successful demonstration of the internal camera functionality. Efforts to improve face detection under these conditions included enhancing illumination and artificially padding the frame borders to create the illusion of a more distant face. For our demonstration purposes, the camera was positioned outside the head. Future work is required to fully achieve the project's initial objectives under these specific conditions.
As a reminder, all final and test code for the model training process, pre-trained models, can be found in the project GitHub page linked in the appendix.

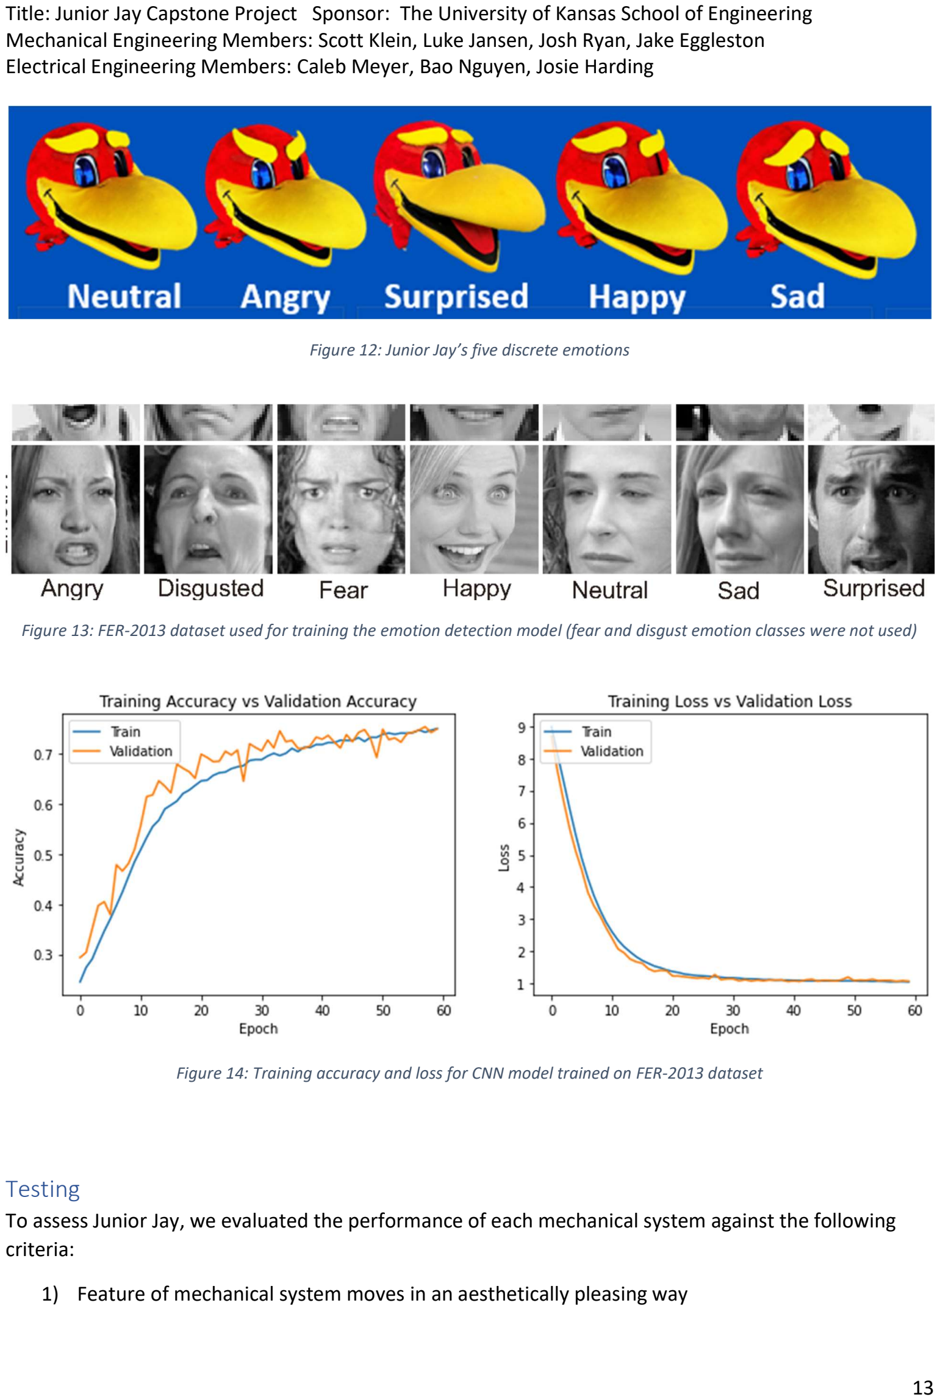
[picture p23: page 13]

Electrical Engineering Members: Caleb Meyer, Bao Nguyen, Josie Harding

13

Figure 12: Junior Jay’s five discrete emotions

Figure 13: FER-2013 dataset used for training the emotion detection model (fear and disgust emotion classes were not used)

Figure 14: Training accuracy and loss for CNN model trained on FER-2013 dataset

### Testing

To assess Junior Jay, we evaluated the performance of each mechanical system against the following criteria:
1) Feature of mechanical system moves in an aesthetically pleasing way

Electrical Engineering Members: Caleb Meyer, Bao Nguyen, Josie Harding

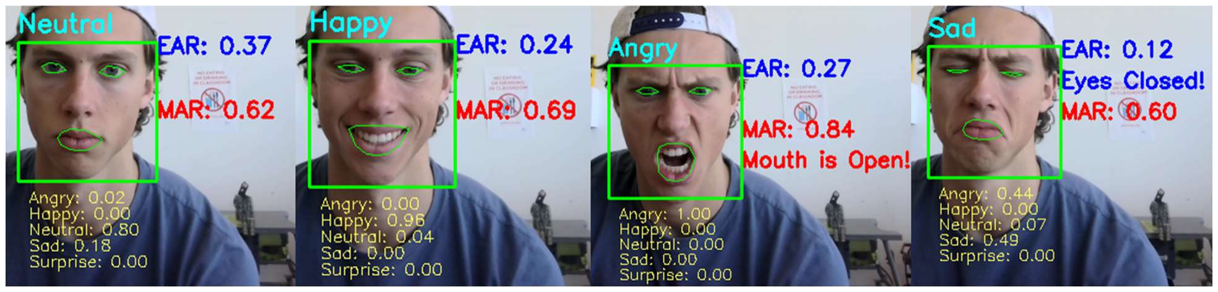
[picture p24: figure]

14

2) Feature of mechanical system moves in a timing comparable to the real-life movement of human features
3) System can operate without fault for 5 minutes
Each system was tested, compared, and iterated until these criteria were met.
In terms of the electrical systems, testing involved troubleshooting all connections to ensure they were permanently connected and maintained control over the mechanical systems for 5 minutes. Also, cooling fans were subjectively measured per use of the user over 5 minutes of testing. 5-minute intervals were repeated for each system until the whole mascot head could simultaneously run together for 5 minutes.
Much testing was done to ensure that the software was able to accurately and consistently predict emotions of a variety of subjects. Model class predictions were plotted to a GUI window on a monitor (figure 15) to easily see exactly how confident the model was in a certain emotion at a certain instance. A key tool employed was manual biasing of certain emotions. For example, the model tended to incorrectly predict “sad” as “angry”, but never the opposite. The solution for this was to artificially bias the program to as to give less weight to predicting “angry”. This allowed sadness to be predicted with much more frequency.

Figure 15: Master script running. Emotion detection (teal) with breakdown of class predictions (yellow), eye state (blue), and mouth state (red) are plotted on a GUI window to give visual feedback for testing purposes.

### Results

The beak, eyebrow, and eyelid mechanical systems were prototyped and iterated upon until its movement looked natural, quick, and could run longer than 5 minutes. The beak could complete one open and close cycle in 0.5 seconds. The eyebrow system could reach various positions in under 0.25 seconds, and could achieve 5 different predefined facial expressions; neutral, happy, mad, sad, surprised. The eyelids were never demonstrated successfully with the whole integrated head, but they were successfully able to complete an open and close cycle in 1.5 seconds during independent testing. The camera and facial recognition software detected various user facial expressions with ease and output a signal to the mechanical systems within 1 second. Furthermore, the camera and facial recognition software could run for longer than 5 minutes. Lastly, the fans were subjectively concluded as adequate over the testing period of 5 minutes.

Electrical Engineering Members: Caleb Meyer, Bao Nguyen, Josie Harding

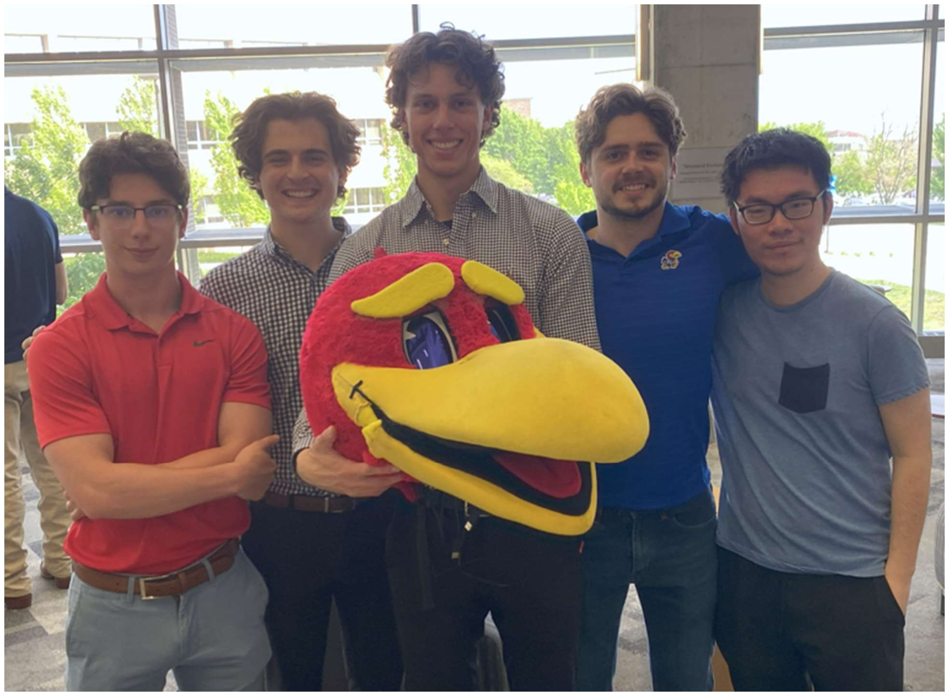
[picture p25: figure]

15

Figure 16: Final product with the team (from right to left): Jake Eggleston, Josh Ryan, Luke Jansen, Scott Klein, and Bao Ngyuen

## Discussion

### Summary of Work

Overall, a Junior Jay mascot was created with expressive capabilities. Junior Jay is equipped with a Raspberry Pi board powered by a 5-volt battery pack, and an external digital camera that acts as an input. Another 5-volt battery pack and 9-volt battery pack, attached to a custom power breakout board, power the rest of the systems of the mascot head. The jaw is equipped with two 45-kilogram servo motors, bracket mounts, and an aluminum frame to move the jaw. The eyelids include an aluminum frame and rod system that spools eyelid fabric by means of a servo motor, belts, and switches. The eyes are made of vacuum formed plastic with layers of film to provide a one-way mirror window. The eyebrows are equipped with two 7 kg micro servo motors each attached to the eyelid frame, links, and fabric covered 3D printed eyebrows. Lastly, 4 micro fans are scattered throughout the helmet to provide cooling.
The culmination of these mechanical systems along with a Raspberry Pi Board, camera, and batteries allows for a mascot head that mirrors multiple facial expressions of the camera user. The eyebrows and jaw of junior jaw worked seamlessly and realistically, with a battery life of about 4 hours. The facial

Electrical Engineering Members: Caleb Meyer, Bao Nguyen, Josie Harding

16

recognition along with the camera were able to detect and interpret facial expressions of most camera users with a response time of 1 second. The operation of the mascot head was comfortable and was adequately cooled. The one-way mirror window design of the eye’s allowed for proper vision and use. Batteries were stored in a backpack worn by the mascot user, which also allowed Junior Jay to be mobile. After testing Junior Jay, the final operating time was close to 3 hours without any issues. While most of the mascot head worked, the eyelids had a short life cycle along with dysfunctional code and were not powered on for the final exposition.
In short, Junior Jay worked well and met all engineering objectives. Junior Jay performed facial expression animation for various human emotions, involved facial recognition of camera users, included a cooling system, was durable and comfortable enough to operate for several hours, and could be easily operated.

### Future Work

While the project has made significant strides in enhancing the functionality and appeal of the university mascots, there remains scope for further development to fully realize the envisioned goals. Future work could focus on several areas to refine and expand the project's achievements:

1. Refinement of Mechanical Systems: Further refinement of the mechanical systems controlling facial expressions is essential. Continuous testing and iteration could lead to more fluid and natural movements, reducing any mechanical lag or stiffness currently present.

### 2. Advanced AI and Machine Learning: Implementing more sophisticated AI algorithms and

machine learning techniques, such as training on a larger dataset or a custom dataset built to our specific needs, could enhance the accuracy and responsiveness of the facial recognition system. Also, work can be done to give more nuanced expressions prediction rather than the simpler discrete expression approach used. This would ensure a more precise and seamless translation of the performer’s expressions to the mascot.
3. Enhanced Cooling Technologies: Although the current cooling system provides basic relief, exploring advanced technologies like phase change materials or more efficient heat exchange mechanisms could offer better temperature regulation, increasing comfort during longer performances or in more extreme weather.

### 4. Integration of Interactive Technologies: Adding interactive technologies such as voice

modulation and responsive sound systems could make the mascots even more engaging. For instance, allowing the mascots to respond vocally to crowd interactions or integrate sound effects linked to their movements could greatly enhance audience interaction.
5. Sustainability and Materials Science: Investigating more sustainable materials and construction techniques that maintain durability while reducing weight could improve the ergonomics and environmental impact of the mascot costumes.
6. Extended Wearability Studies: Conducting extended wearability studies to gather data on the performer's comfort and suit ergonomics over longer periods can provide insights into necessary adjustments and improvements.

Electrical Engineering Members: Caleb Meyer, Bao Nguyen, Josie Harding

17

### 7. Scalability and Transferability: Finally, considering how these enhancements can be

standardized and transferred to other mascot programs could broaden the impact of the project. Developing a modular system that can be customized and adapted to different mascots could make these advancements more accessible to other institutions.
8. Foolproof electrical safety measures: A mechanical cover should be added to cover the power bus to protect against accidental contact and reduce the risk of short circuits. Additionally, wiring may be optimally routed inside the head wall to minimize exposure and vulnerability. Safety devices such as fuses, and micro-circuit breakers will be incorporated to prevent electrical overloads and potential hazards.

These areas of future work would not only address the remaining challenges but also push the boundaries of what is possible in mascot design and performance, potentially setting new industry standards.

Electrical Engineering Members: Caleb Meyer, Bao Nguyen, Josie Harding

18

## Appendices

### References

"Bird Anatomy for Animators." Journal of Animation Studies.
US Patent CN201780082251.0A, " Social robot with environmental control features." US Patent 11592659, “Optical viewfinder for costume heads.”
AnimationResources.org. "Bird Animation Tutorials."
Williams, Richard. "The Animator's Survival Kit."
International Animation Society (IAS). "Standards for Non-Human Character Animation."

### Drawings

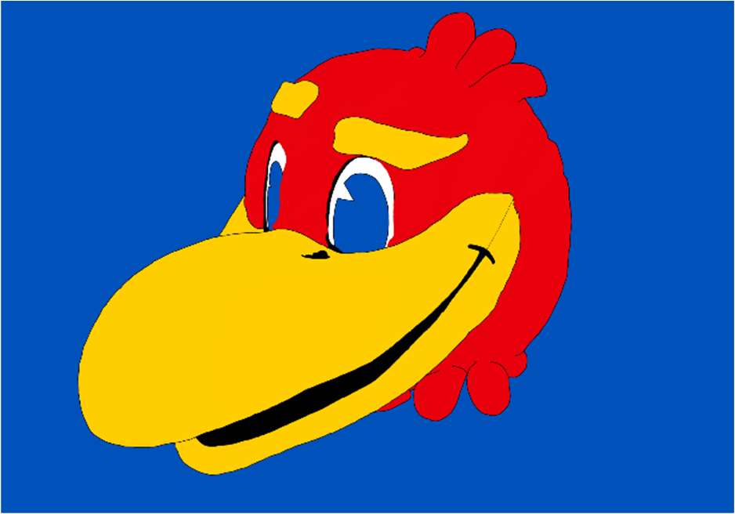
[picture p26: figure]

Figure A1. Head concept 1

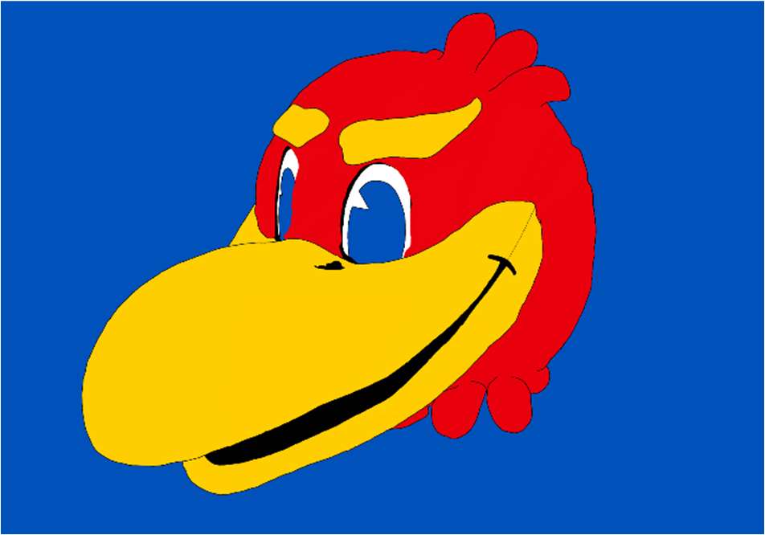
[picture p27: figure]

Figure A2. Head concept 2

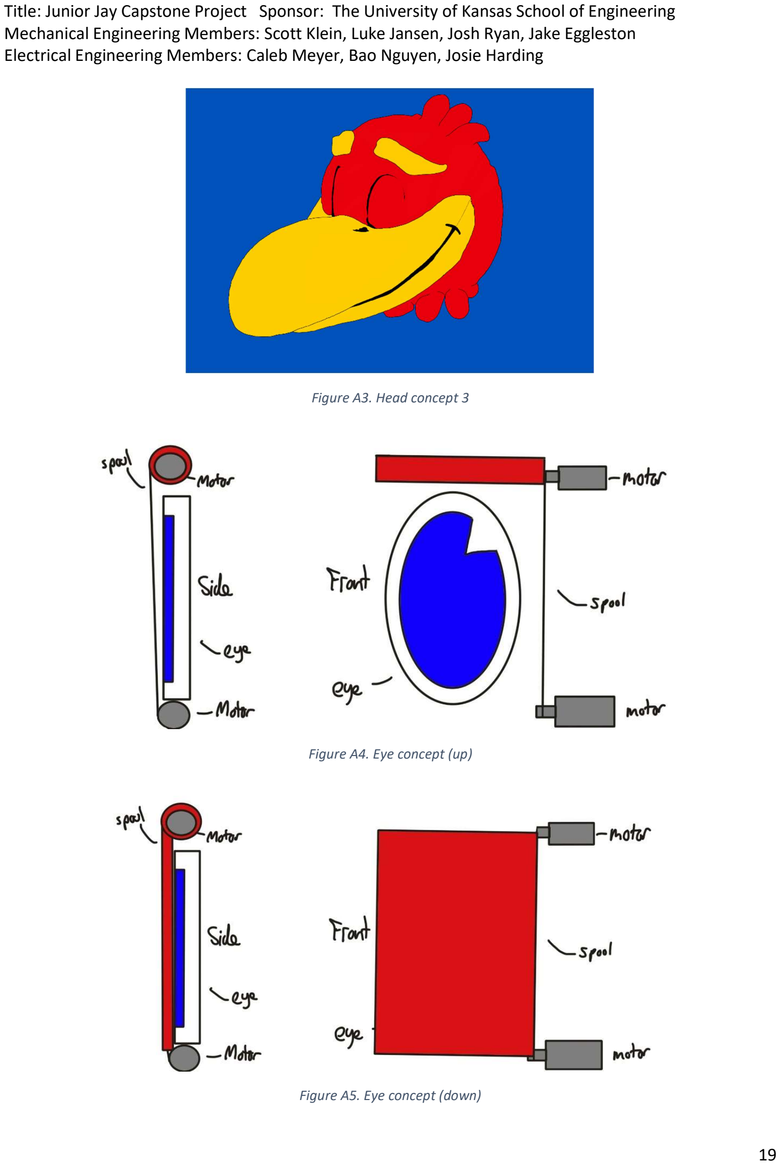
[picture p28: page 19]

Electrical Engineering Members: Caleb Meyer, Bao Nguyen, Josie Harding

19

Figure A3. Head concept 3

Figure A4. Eye concept (up)

Figure A5. Eye concept (down)

Electrical Engineering Members: Caleb Meyer, Bao Nguyen, Josie Harding

20

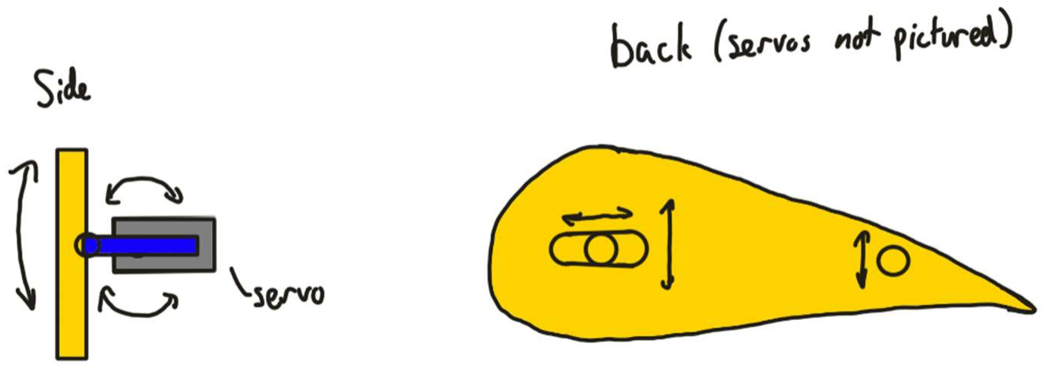
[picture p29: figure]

Figure A6. Eyebrow concept

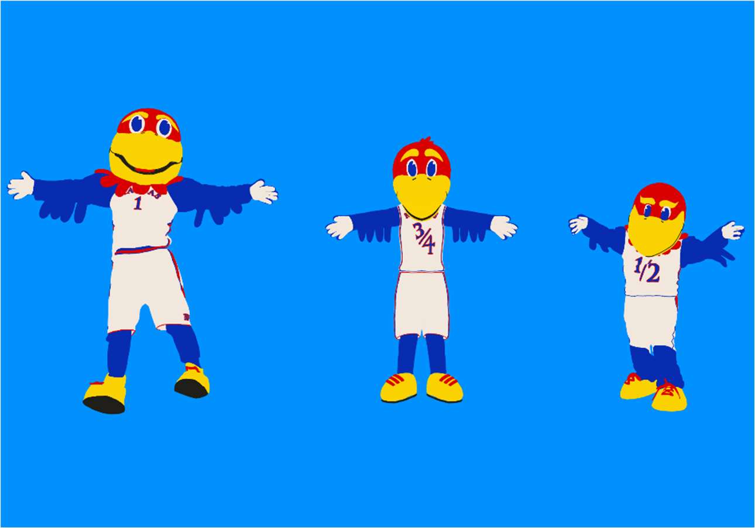
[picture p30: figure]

Figure A7. Full mascot suit concept (Big Jay, Junior Jay, Baby Jay)

### Code

All code used for this project can be conveniently found on the following GitHub repository: https://github.com/lujan002/Animatronic-Mascot-Suit

Electrical Engineering Members: Caleb Meyer, Bao Nguyen, Josie Harding

21

### Key Equipment

List the major equipment with supplier and part numbers – only things that were unique and critical
Item | Vendor | Part Number
Arducam USB Camera (Low Light, 160° Wide Angle) | Amazon | B07ZS75KZR
45 kg High Torque Servo | Amazon | B0C69BXL6V
Injora 7kg digital servo | Amazon | B0BLBMVYCW
Raspberry Pi 4 Model B - 8GB RAM | Adafruit | 4564
Pisoo 65W Power Bank | Amazon | B0C5D1JR2K

### Sponsor Contact Information

KU Athletics Mascot Coach: Brian Carpenter - bcarpenter@ku.edu
KU School of Engineering: Dr. Pourladian - bamdadpourladian@ku.edu

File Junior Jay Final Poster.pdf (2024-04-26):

# Junior Jay

ME: Luke Jansen, Scott Klein, Josh Ryan, Jake Eggleston EECS: Bao Nguyen, Caleb Meyer, Josie Harding

# Facial Detection Software

### Develop a Jayhawk mascot animatronic with dynamic facial expressions for better

live audience interaction,

### controlled by the wearer's

facial movements.

- Python script captures video frames, detects faces, predicts facial expression, and sends signal to adjust servo angles to mimic detected expression.
- Custom machine learning model trained on the FER 2013 dataset for emotion recognition. Eye/mouth aspect ratio calculated to determine if open/closed.
- Difficulties detecting face in dark, close-up environment inside the head—even with low light, wide angle camera.

# Electrical System

- 50,000mAh battery pack chosen for 2hr. lifetime, 5-20V output.
- HUSB238 draws 5V, 9V from battery, custom power bus distributes 9V power to two beak servos, 5V to other six servos.
- Power resistors protect system by limiting current flow.
- Raspberry Pi runs facial detection software and sends signal to servos over GPIO pins.
- Optional LED panel installed in head indicates detected emotion to wearer.

Raspberry Pi 4

Project Goal | Mechanical Mechanisms
| Beak: • Goal: Open/close to simulate smile, shock. • Two high-torque servo motors running on 9V move lightweight Al frame fixed to beak. • Servo choice driven by requirement to counter beak weight of 1.5 lbs. with center of gravity centered 9 in. away (13.5 lbs·in). Eyebrows: • Goal: Rotate to display nuanced emotions. • 3-bar linkage consisting of fixed arm, slider arm, and eyebrow, uses servo rotation to pivot eyebrow. • Servos mounted neatly on eyelid frame inside head, with shafts protruding through forehead that spin links. Eyelids: • Goal: Open/close to simulate blinking. • Custom thermoformed plastic coated with one-way mirror film ensures internal components cannot be seen from outside. • Belt-driven mechanism spins stitched-on fabric (eyelid) by continuous rotation servo. • Fabric spools at top so wearer’s vision is not obscured when in open position. • Limit switches tripped by belt send signal to shut off servo when eyelid is fully open/closed.

Custom 5V/9V
Power Bus w/
Power Resistors
HUSB238 Power
Delivery Breakout

Special thanks to KU Athletics for making this project possible by donating a retired Baby Jay head.

Arducam USB Camera
(Low Light, 160° Wide Angle)

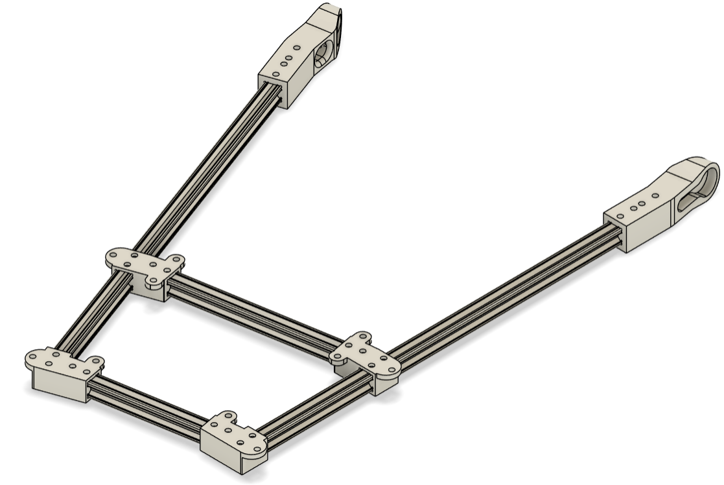
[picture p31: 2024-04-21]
BeakCAD.png

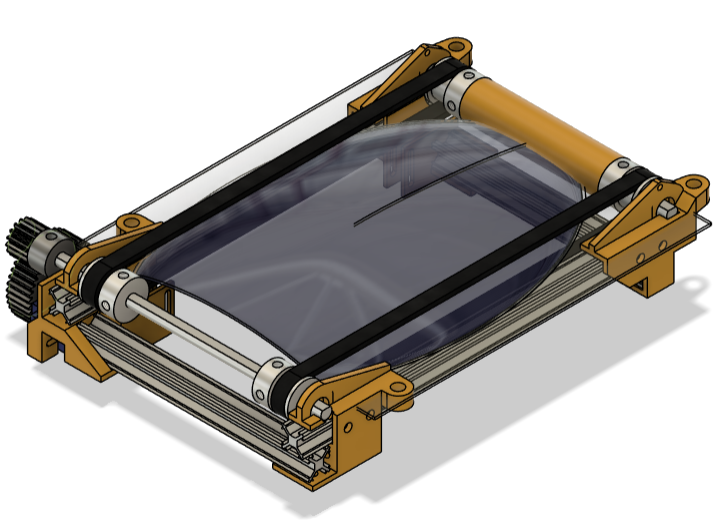
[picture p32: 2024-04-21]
EyelidCAD.png

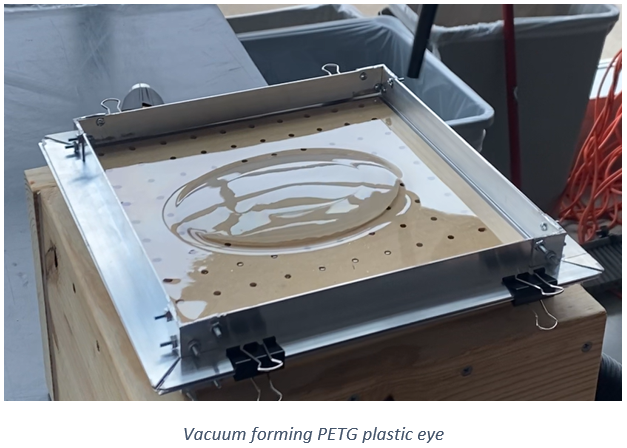
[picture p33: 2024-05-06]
VaccumFormedEye.png

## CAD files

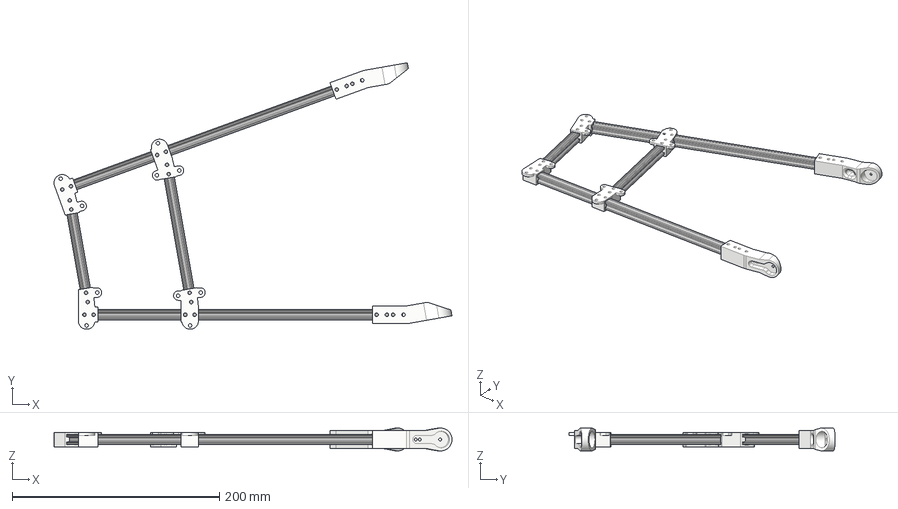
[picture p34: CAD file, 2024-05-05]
3D Parts/Beak/models/beak_frame_assembly.step
384.4 x 257.4 x 22.0 mm
jaw_bracket_middle_v2-L
jaw_bracket_middle_v2-R
jaw_bracket_end_L
jaw_bracket_end_R
servo_direct_to_beak_v4-L
servo_direct_to_beak_v4-R

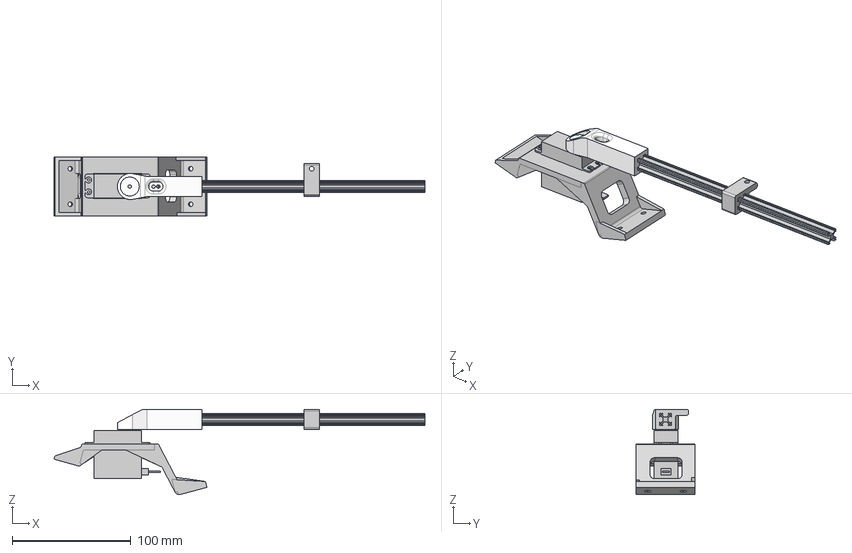
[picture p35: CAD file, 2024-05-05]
3D Parts/Beak/models/beak_servo_mount.step
312.9 x 50.0 x 71.9 mm
AL Extrusion
Servo
Servo Mount
AL Ext. Mount

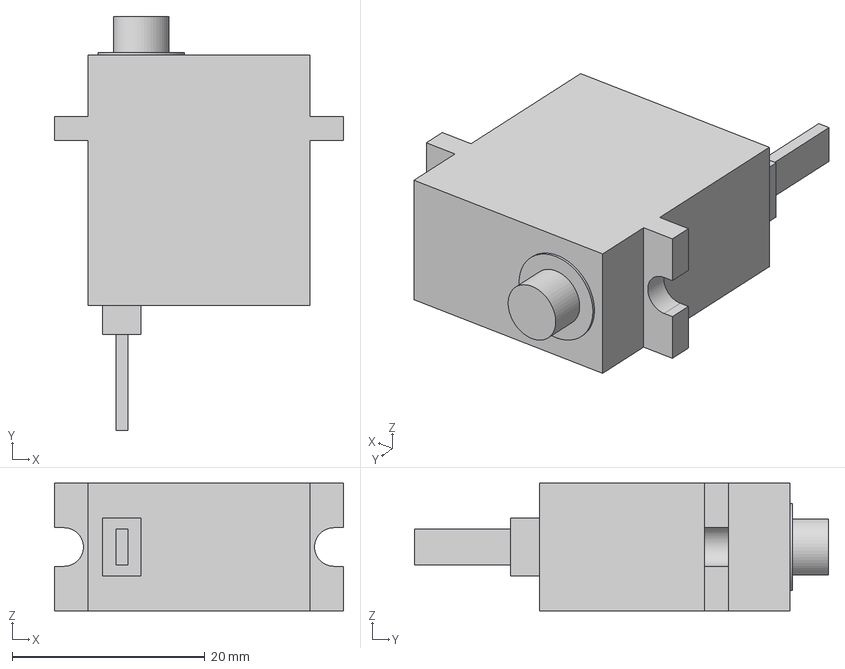
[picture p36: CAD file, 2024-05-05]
3D Parts/Eyebrow/models/servo_7kg.stp
30.0 x 43.0 x 13.2 mm

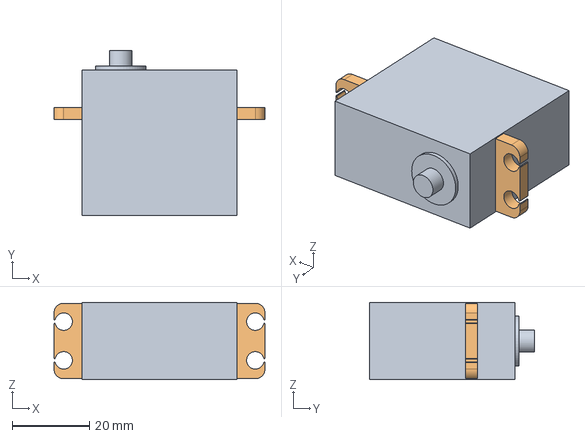
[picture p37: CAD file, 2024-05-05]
3D Parts/Beak/models/servo_45kg.stp
54.5 x 42.5 x 20.0 mm

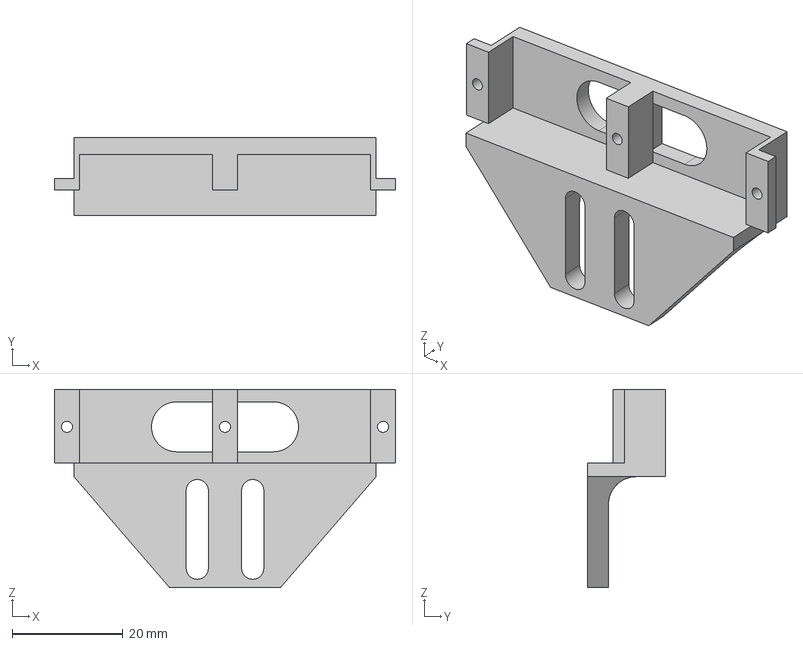
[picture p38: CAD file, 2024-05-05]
3D Parts/Eyebrow/models/eyebrow_servo_mount.stp
61.5 x 14.0 x 35.8 mm

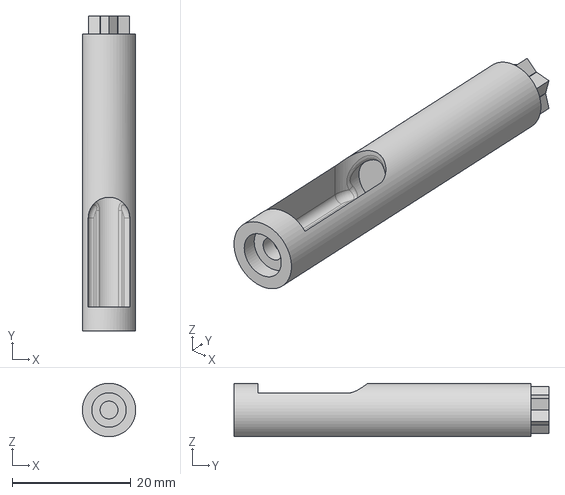
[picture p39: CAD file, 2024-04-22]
3D Parts/Eyebrow/models/servo_extension_50mm.step
8.99 x 53.0 x 9.00 mm

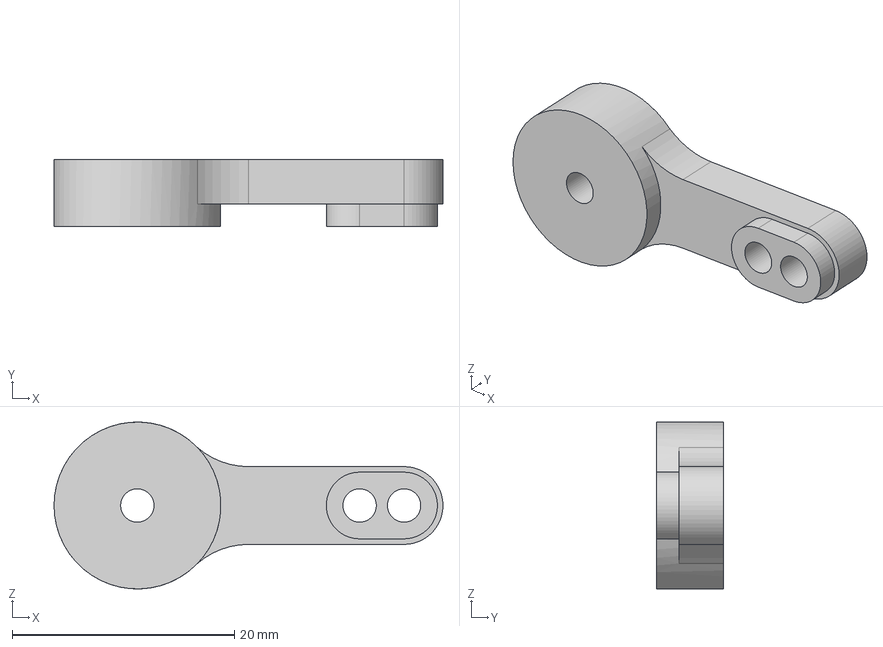
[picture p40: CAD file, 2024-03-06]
3D Parts/Beak/models/beak_servo_arm.step
35.0 x 6.00 x 15.0 mm

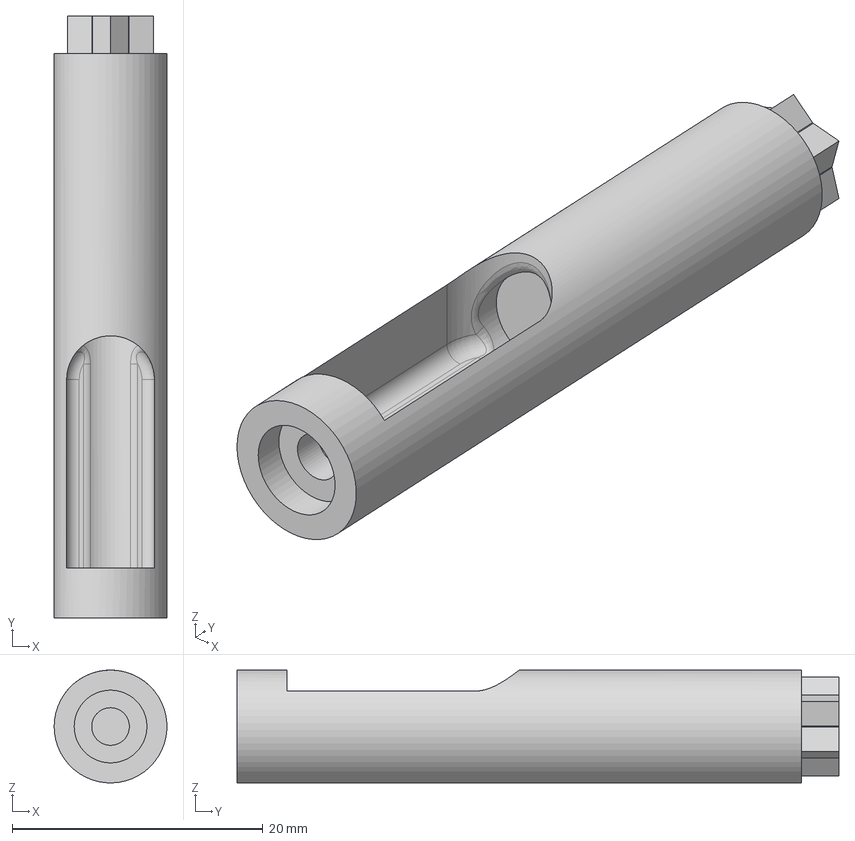
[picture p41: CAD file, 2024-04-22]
3D Parts/Eyebrow/models/servo_extension_45mm.step
8.99 x 48.0 x 9.00 mm

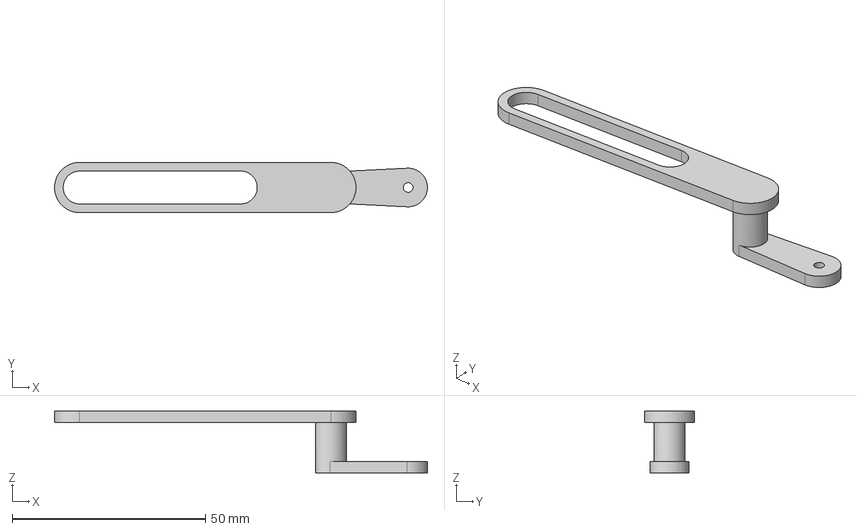
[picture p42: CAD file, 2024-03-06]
3D Parts/Eyebrow/models/Link2b.step
96.5 x 13.0 x 16.0 mm

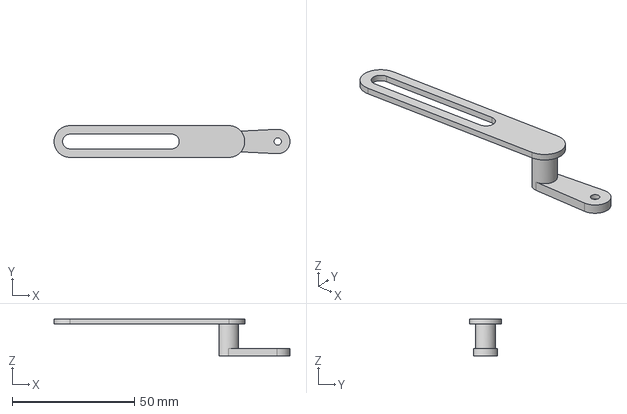
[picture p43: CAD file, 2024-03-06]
3D Parts/Eyebrow/models/Link2c.step
96.5 x 13.0 x 15.0 mm

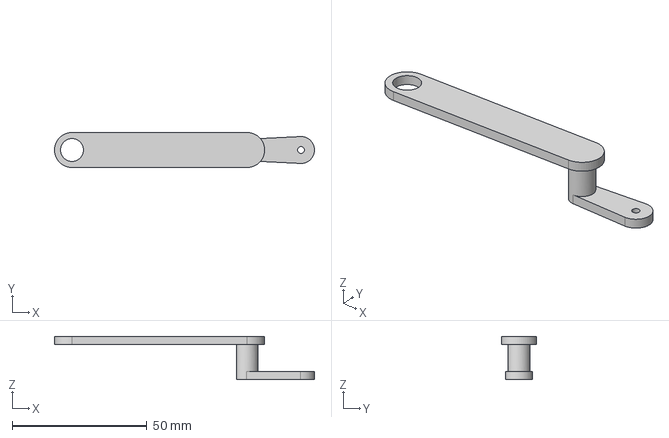
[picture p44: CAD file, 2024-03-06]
3D Parts/Eyebrow/models/Link1b.step
96.5 x 13.0 x 16.0 mm

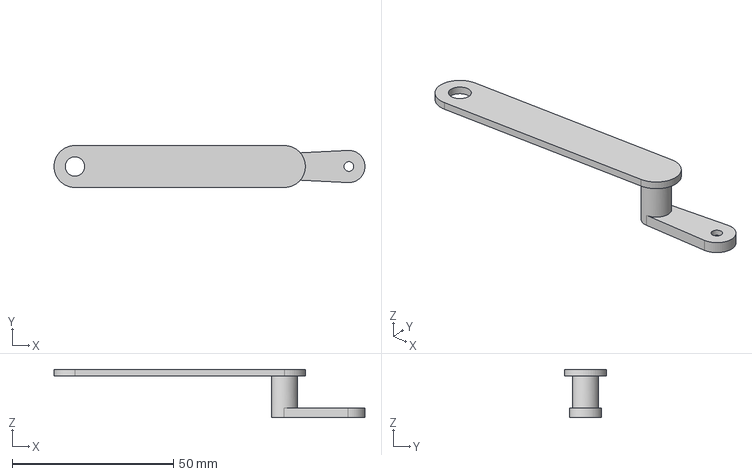
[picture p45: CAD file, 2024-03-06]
3D Parts/Eyebrow/models/Link1c.step
96.5 x 13.0 x 15.0 mm

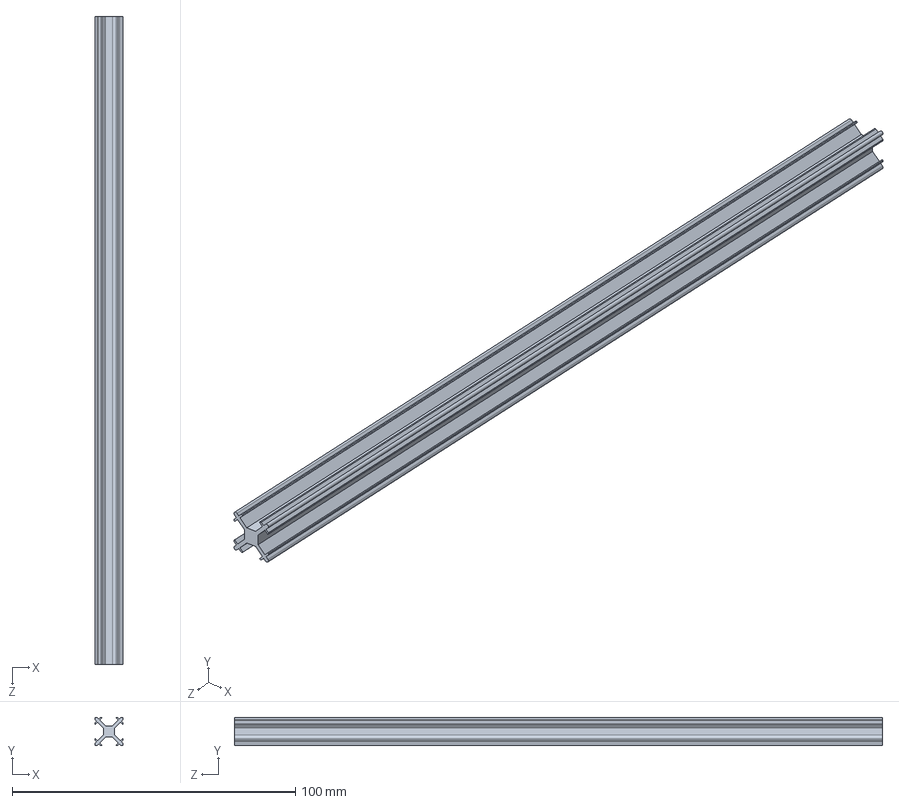
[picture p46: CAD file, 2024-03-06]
3D Parts/Beak/models/1959N13_Miniature T-Slotted Framing.STEP
10.0 x 10.0 x 228.6 mm

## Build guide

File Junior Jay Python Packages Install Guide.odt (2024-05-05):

Junior Jay Python Packages Install Guide

Steps to install dlib

(according to: https://pyimagesearch.com/2017/03/27/how-to-install-dlib/)

(install dlib pre-reqs)

sudo apt-get install build-essential cmake

sudo apt-get install libgtk-3-dev

sudo apt-get install libboost-all-dev

(create virtual environment)

python3 -m venv venv

source venv/bin/activate

pip install numpy

pip install scipy

pip install scikit-image

pip install dlib (this can take a loooong time, just wait)

Install other required packages

pip install imutils

pip install opencv-python

pip install serial

pip install RPi.GPIO

pip install pigpio (run “sudo pigpiod” after each system reboot to initialize pigpio)

pip install mtcnn (for better facial detection)

In VSCode, change interpreter path to newly created venv

In VSCode, hit Ctrl+Shift+P then type “Python: Select Interpreter” and enter the following path to the venv: /home/juniorjay/venv/bin/python

FER install guide

python -m venv fer_venv (create venv in /home/user)

cd /home/user/fer_venv/Scripts/

activate (venv is now active, proceed to package install)

pip install opencv-python

sudo apt-get install libhdf5-dev (required for tensorflow)

pip install tensorflow (Note here we are installing tensorflow-cpu)

Startup master-script on boot

echo "/home/lujan002/Repositories/jj_venv/bin/python3.11 "/home/lujan002/Repositories/Animatronic-Mascot-Suit/JJ Code/master-script.py" " >> ~/.bashrc

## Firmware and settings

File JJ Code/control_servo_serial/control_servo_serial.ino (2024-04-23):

#include <Servo.h>

Servo servo1;
Servo servo2;
Servo servo3;
Servo servo4;
// Add more servos as needed

void setup() {
  Serial.begin(9600);
  servo1.attach(10);
  servo1.write(90);
  servo2.attach(11);
  servo2.write(90);  
  servo3.attach(12);
  servo3.write(90);
  servo4.attach(13);
  servo4.write(90);
  //Attach more servos as needed
}

void loop() {
  // Check if data is available to read from the serial buffer
  if (Serial.available()) {
    // Read the incoming data as a string until a newline character ('\n') is encountered
    String data = Serial.readStringUntil('\n');

    int firstCommaIndex = data.indexOf(',');
    int secondCommaIndex = data.indexOf(',', firstCommaIndex + 1);
    int thirdCommaIndex = data.indexOf(',', secondCommaIndex + 1);

    // Extract servo values from the data string
    int servo1Value = data.substring(0, firstCommaIndex).toInt();
    int servo2Value = data.substring(firstCommaIndex + 1, secondCommaIndex).toInt();
    int servo3Value = data.substring(secondCommaIndex + 1, thirdCommaIndex).toInt();
    int servo4Value = data.substring(thirdCommaIndex + 1).toInt(); // To the end of the string
    
    // Send the integer values to the respective servos to set their positions
    servo1.write(servo1Value);
    servo2.write(servo2Value);
    servo3.write(servo3Value);
    servo4.write(servo4Value);
  }
}

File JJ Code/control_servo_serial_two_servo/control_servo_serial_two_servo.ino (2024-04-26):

const int limitSwitchPin = 2; // Pin connected to the limit switch

volatile int switchState = HIGH; // volatile keyword is used as this variable changes inside an interrupt

void setup() {
  Serial.begin(9600);
  pinMode(limitSwitchPin, INPUT_PULLUP); // Use internal pull-up resistor
  attachInterrupt(digitalPinToInterrupt(limitSwitchPin), toggleSwitch, CHANGE); // Attach interrupt
}

void loop() {
  if (switchState == LOW) {
    Serial.println("Low"); // Pressed
  } else {
    Serial.println("High"); // Not pressed
  }
  delay(100); // Delay to reduce serial output speed
}

void toggleSwitch() {
  switchState = digitalRead(limitSwitchPin); // Read the new state of the limit switch
}

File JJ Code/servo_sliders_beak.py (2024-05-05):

# -*- coding: utf-8 -*-
"""
Created on Thu Feb 15 16:34:46 2024

Program to test movement of the beak using Raspberry Pi GPIO.
Slider 1 and 2 have an inverse relationship centered around 89 degrees (due to physical calibration)
Sliders 3 and 4 are irrelevant and just meant for lazy compatibility with a previous Arduino version.
"""

import tkinter as tk
from tkinter import ttk
from gpiozero import Servo
from time import sleep

# Define GPIO pins for Servos
servo1_pin = 5  # GPIO pin 17 for Servo 1
servo2_pin = 6 # GPIO pin 18 for Servo 2

# Setup Servo devices
servo1 = Servo(servo1_pin)
servo2 = Servo(servo2_pin)

def update_servos():
    # Convert slider values from scale to -1 to 1 for Servo
    servo1_value = slider_to_servo(slider1.get(), 96, 111)
    servo2_value = slider_to_servo(slider2.get(), 67, 82)
    servo1.value = servo1_value
    servo2.value = servo2_value
    sleep(0.1)  # Add a small delay to allow servo to move

def slider_to_servo(value, min_val, max_val):
    """Convert slider value to -1 to 1 scale for gpiozero Servo."""
    return (value - min_val) / (max_val - min_val) * 2 - 1

def update_slider1(event):
    value1 = slider1.get()
    label1.config(text=f"Value: {value1}")
<<<<<<< HEAD
    slider2.set(178 - value1)
    update_slider2(None)
    update_servos()
=======
    # Update slider2 in the opposite direction
    slider2.set(178 - value1)
    update_slider2(None)  # Update slider2's label and send to Arduino
    send_to_arduino()
>>>>>>> 35ba36025ccfcfcd19106c84bc3b9c439ef26831

def update_slider2(event):
    value2 = slider2.get()
    label2.config(text=f"Value: {value2}")
    if event:
        slider1.set(178 - value2)
<<<<<<< HEAD
        update_slider1(None)
    update_servos()
=======
        update_slider1(None)  # Update slider1's label and send to Arduino
    send_to_arduino()
>>>>>>> 35ba36025ccfcfcd19106c84bc3b9c439ef26831

root = tk.Tk()
root.title("Servo Control")

<<<<<<< HEAD
=======
# LEFT BEAK SERVO IS SERVO 1 (PIN 10)
# Create the first slider
>>>>>>> 35ba36025ccfcfcd19106c84bc3b9c439ef26831
slider1 = ttk.Scale(root, from_=85, to=111, orient='horizontal')
slider1.pack()
slider1.set(98)  # Initial value adjusted
label1 = tk.Label(root, text="Value: 98")
label1.pack()
slider1.bind("<B1-Motion>", update_slider1)

<<<<<<< HEAD
=======
# RIGHT BEAK SERVO IS SERVO 2 (PIN 11)
# Create the second slider
>>>>>>> 35ba36025ccfcfcd19106c84bc3b9c439ef26831
slider2 = ttk.Scale(root, from_=67, to=82, orient='horizontal')
slider2.pack()
slider2.set(80)  # Initially set to opposite of slider1
label2 = tk.Label(root, text="Value: 80")
label2.pack()
slider2.bind("<B1-Motion>", update_slider2)

root.mainloop()

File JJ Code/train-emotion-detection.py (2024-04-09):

# -*- coding: utf-8 -*-
"""
Created on Tue Apr  2 21:52:55 2024

@author: 20Jan
"""

import numpy as np # linear algebra
import pandas as pd # data processing, CSV file I/O (e.g. pd.read_csv)
import os
#for dirname, _, filenames in os.walk('/kaggle/input'):
    #for filename in filenames:
        #print(os.path.join(dirname, filename))
import matplotlib.pyplot as plt
import seaborn as sns
import tensorflow as tf
import keras
from keras.preprocessing import image
from keras.models import Sequential
from keras.layers import Conv2D, MaxPool2D, Flatten,Dense,Dropout,BatchNormalization
from tensorflow.keras.preprocessing.image import ImageDataGenerator
import cv2
from tensorflow.keras.applications import VGG16, InceptionResNetV2
from keras import regularizers
from tensorflow.keras.optimizers import Adam,RMSprop,SGD,Adamax
from sklearn.utils.class_weight import compute_class_weight

#%%
train_dir = "/Users/20Jan/Junior Jay Capstone/JJ Code/fer-dataset/train" #passing the path with training images
test_dir = "/Users/20Jan/Junior Jay Capstone/JJ Code/fer-dataset/test"   #passing the path with testing images

img_size = 48 #original size of the image

"""
Data Augmentation
--------------------------
rotation_range = rotates the image with the amount of degrees we provide
width_shift_range = shifts the image randomly to the right or left along the width of the image
height_shift range = shifts image randomly to up or below along the height of the image
horizontal_flip = flips the image horizontally
rescale = to scale down the pizel values in our image between 0 and 1
zoom_range = applies random zoom to our object
validation_split = reserves some images to be used for validation purpose
"""

train_datagen = ImageDataGenerator(#rotation_range = 180,
                                         width_shift_range = 0.1,
                                         height_shift_range = 0.1,
                                         horizontal_flip = True,
                                         rescale = 1./255,
                                         #zoom_range = 0.2,
                                         validation_split = 0.2
                                        )
validation_datagen = ImageDataGenerator(rescale = 1./255,
                                         validation_split = 0.2)

"""
Applying data augmentation to the images as we read 
them from their respectivve directories
"""
train_generator = train_datagen.flow_from_directory(directory = train_dir,
                                                    target_size = (img_size,img_size),
                                                    batch_size = 64,
                                                    color_mode = "grayscale",
                                                    class_mode = "categorical",
                                                    subset = "training"
                                                   )
validation_generator = validation_datagen.flow_from_directory( directory = test_dir,
                                                              target_size = (img_size,img_size),
                                                              batch_size = 64,
                                                              color_mode = "grayscale",
                                                              class_mode = "categorical",
                                                              subset = "validation"
                                                             )

"""
Weighting the loss function is a strategy to make the model pay more attention 
to samples from underrepresented classes by assigning higher weights to their loss contributions.
"""
# Extract class labels from the training generator
y_train = train_generator.classes

# `class_indices` has class names as keys and their corresponding labels as values. We need the reverse mapping.
label_to_class = {v: k for k, v in train_generator.class_indices.items()}

# Calculate class weights
class_weights = compute_class_weight(
    class_weight='balanced',
    classes=np.unique(y_train),
    y=y_train)

# Map computed class weights back to the corresponding classes in 'train_generator.class_indices'
class_weights_dict = {label_to_class[i]: weight for i, weight in enumerate(class_weights)}

"""
Modeling


model = Sequential()
model.add(Conv2D(filters = 64,kernel_size = (3,3),padding = 'same',activation = 'relu',input_shape=(img_size,img_size,1)))
model.add(MaxPool2D(pool_size = 2,strides = 2))
model.add(BatchNormalization())

model.add(Conv2D(filters = 128,kernel_size = (3,3),padding = 'same',activation = 'relu'))
model.add(MaxPool2D(pool_size = 2,strides = 2))
model.add(BatchNormalization())
model.add(Dropout(0.25))

model.add(Conv2D(filters = 128,kernel_size = (3,3),padding = 'same',activation = 'relu'))
model.add(MaxPool2D(pool_size = 2,strides = 2))
model.add(BatchNormalization())
model.add(Dropout(0.25))

model.add(Conv2D(filters = 256,kernel_size = (3,3),padding = 'same',activation = 'relu'))
model.add(MaxPool2D(pool_size = 2,strides = 2))
model.add(BatchNormalization())

model.add(Flatten())
model.add(Dense(units = 128,activation = 'relu',kernel_initializer='he_normal'))
model.add(Dropout(0.25))
model.add(Dense(units = 64,activation = 'relu',kernel_initializer='he_normal'))
model.add(BatchNormalization())
model.add(Dropout(0.25))
model.add(Dense(units = 32,activation = 'relu',kernel_initializer='he_normal'))
model.add(Dense(7,activation = 'softmax'))

"""

model= tf.keras.models.Sequential()
model.add(Conv2D(32, kernel_size=(3, 3), padding='same', activation='relu', input_shape=(48, 48,1)))
model.add(Conv2D(64,(3,3), padding='same', activation='relu' ))
model.add(BatchNormalization())
model.add(MaxPool2D(pool_size=(2, 2)))
model.add(Dropout(0.25))

model.add(Conv2D(128,(5,5), padding='same', activation='relu'))
model.add(BatchNormalization())
model.add(MaxPool2D(pool_size=(2, 2)))
model.add(Dropout(0.25))
    
model.add(Conv2D(512,(3,3), padding='same', activation='relu', kernel_regularizer=regularizers.l2(0.01)))
model.add(BatchNormalization())
model.add(MaxPool2D(pool_size=(2, 2)))
model.add(Dropout(0.25))

model.add(Conv2D(512,(3,3), padding='same', activation='relu', kernel_regularizer=regularizers.l2(0.01)))
model.add(BatchNormalization())
model.add(MaxPool2D(pool_size=(2, 2)))
model.add(Dropout(0.25))

model.add(Flatten()) 
model.add(Dense(256,activation = 'relu'))
model.add(BatchNormalization())
model.add(Dropout(0.25))
    
model.add(Dense(512,activation = 'relu'))
model.add(BatchNormalization())
model.add(Dropout(0.25))

model.add(Dense(5, activation='softmax'))

model.compile(
    optimizer = Adam(learning_rate=0.0001), 
    loss='categorical_crossentropy', 
    metrics=['accuracy']
  )

epochs = 60
batch_size = 64

model.summary()
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

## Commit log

2024-03-27 added cv code
    [al_extrusion_clip.stl, al_extrusion_servo_bracket.stl, al_extrusion_servo_bracket_v2.stl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]
2024-03-27 first commit from raspberry pi
2024-04-07 updating after succesful emotion detection test
    [servo_direct_to_beak v3.f3d]
2024-04-09 adding vc pcb, model 3, test code for eye/mouth detection
    [voltage_converter.brd, voltage_converter.sch]
2024-04-09 updated readme with pcb documentation
2024-04-09 moved pcb png's to the root folder
2024-04-12 consolidated facial detection, added battery_basket, new voltage converter board
    [battery_basket.stl, spacers v1.stl, voltage_converter.brd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]
2024-04-13 adding two servo slider script
2024-04-13 added led outputs for emotion detection
2024-04-20 changing combined script v8 to add arduino serial integration
2024-04-20 added new PCBs, eyelid test, arduino case
    [ArduinoCase1.stl, ArduinoCase2.stl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]
2024-04-21 splitting v8 into arduino and RPi versions, renaming RPi scripts
2024-04-21 adding 3D parts
    [LightBoxBase v2.stl, LightBoxBase.stl, LightBoxLid.stl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]
2024-04-22 adding servo shaft 3D files
    [ServoExtensionv3_45mm v1.step, ServoExtensionv3_45mm v1.stl, ServoExtensionv3_50mm v1.step]
2024-04-22 adding new battery basket
    [battery_basketv2 v1.stl]
2024-04-22 adding camera 3D mounts
    [Cam1.stl, Cam2.stl, Cam3.stl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]
2024-04-24 reorgainizing 3D Parts Files
    [ArduinoCase1.stl, ArduinoCase2.stl, CAM+loft.f3d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]
2024-04-26 adding Scott's pictures, poster, electrical diagram
    [Electronic+Mounts.stp, Power Bus Mount v2 v1.stl, Power Bus Mount v3 v1.stl]
2024-05-05 test removal cached files
    [1959N13_Miniature T-Slotted Framing.STEP, 50kgServo.step, 7kg Servo.step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]
2024-05-05 adding back files???
    [1959N13_Miniature T-Slotted Framing.STEP, 50kgServo.step, 7kg Servo.step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]
2024-05-05 rm all and pushing with only essential files
    [1959N13_Miniature T-Slotted Framing.STEP, 50kgServo.step, 7kg Servo.step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]
2024-05-05 Committing changes to Junior Jay Python Packages Install Guide.odt
    [ArduinoCase1.stl, ArduinoCase2.stl, Cam1.stl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]
2024-05-05 trying rm cached again
    [ArduinoCase1.stl, ArduinoCase2.stl, Cam1.stl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]
